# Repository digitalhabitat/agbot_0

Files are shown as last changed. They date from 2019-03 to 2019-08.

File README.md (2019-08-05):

# agbot_0

IUPUI's robot for the 2019 Mining for Microbes and Microfauna Agbot Challenge

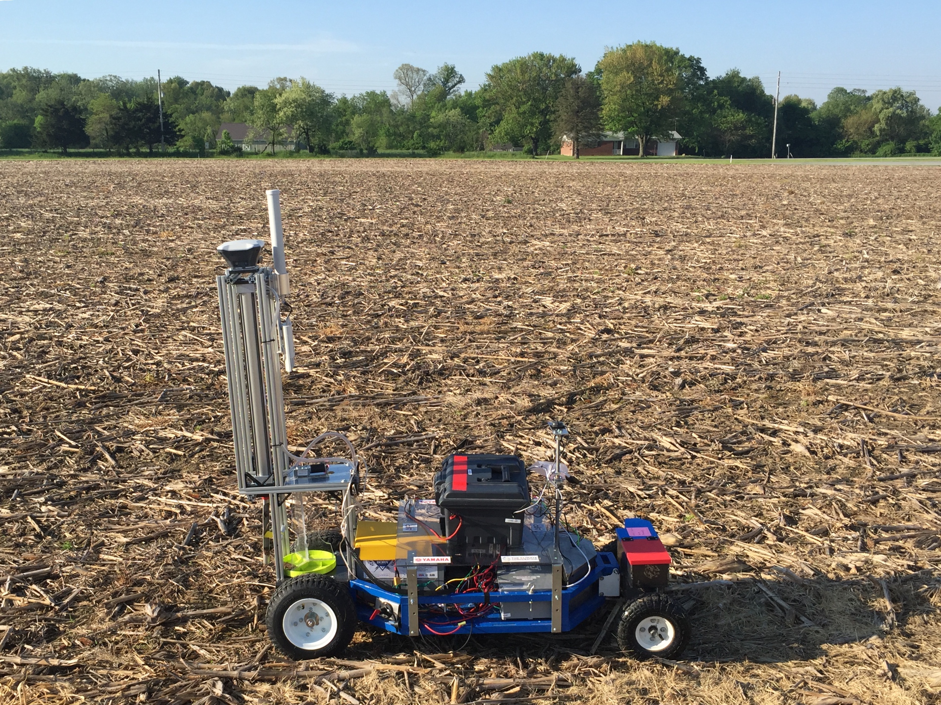
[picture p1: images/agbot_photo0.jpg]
AgBot Photo


## Quick start up

To get the agbot moving perform the following steps

0. Switch on the 12 volt Logic battery by fliping the amber rocker switch inside the tool box encolsure.
1. Turn on the Nvidia TX2 by pressing the right most button. (Green LED on TX2 will light)
2. Connect a computer or phone to the TX2 hotspot or the local wifi 
3. Switch on the AgBot's main power by turning the red mounted E-Switch. (Clockwise) ***THIS IS THE ONBOARD EMERGENCY STOP***
4. Switch on the *Lejin Wireless Relay* power located on the Power Box. (White LED on Wireless relay box will light)
5. On the *Lejin Wireless Remote* press button 1. (White LED on Power Box will light). ***THIS IS THE WIRELESS EMERGENCY STOP***
6. Connect to the TX2 via SSH `ssh nvidia@tegra-ubuntu` (If using a phone use the Terminus App)
7. Turn on the PS4 controller
8. In the terminal enter `checkusb` (This verifies the drive and steering system is ready)
9. In the terminal enter `roslaunch agbot_0 rc.launch` ( Ctrl-C to terminate program)
10. Holding ✕... To drive forward gently press R2. To drive reverse gently press L2. Use left joystick to steer.
11. On the *Lejin Wireless Remote* button 2 will close the solenoid for the air tank to build pressure (Not necessary to penetrate soft soil). 
Button 3 will extend/retract the soil probe.
## Table of Contents

[Precautions and Troubleshooting](https://github.com/digitalhabitat/agbot_0#precautions-and-troubleshooting)

[Local Machine Setup](https://github.com/digitalhabitat/agbot_0#local-machine-setup)

[ROS Packages & Launch files (To run on the agbot runing roscore)](https://github.com/digitalhabitat/agbot_0#ros-packages--launch-files-to-run-on-the-agbot-runing-roscore)

[ROS Packages & Launch files (To run on remote PC)](https://github.com/digitalhabitat/agbot_0#ros-packages--launch-files-to-run-on-remote-pc)

[Main System and Hardware Devices](https://github.com/digitalhabitat/agbot_0#main-systems-and-hardware-devices)

[Abstract Diagram](https://github.com/digitalhabitat/agbot_0#abstract-hardware-diagram)

[Wiring Diagram](https://github.com/digitalhabitat/agbot_0#wiring-diagram)

## Precautions and Troubleshooting

+ The agbot does not stop moving or shows delayed control
	+ The Drive motors will go into a run away state if the wheel encoders are disconnected or intermittent. Ensure that the wheel encoder wire connections are properly attached and secure. Verify safe functionality on a jack stand before operating on the the lab floor. Always be ready to press button 1 on the wireless relay remote to activate the Emergency Stop in case this event occurs. ***NEVER STAND DIRECTLY IN FRONT OR BEHIND THE AGBOT***
	+ The PID controller configuration may need additional tunning. See [BasicMicro Motion Studio](https://www.basicmicro.com/downloads)
	+ Delayed control around 1-2 sec at worst is typical.

+ `ssh nvidia@tegra-ubuntu` is not working
	+ The IP address of the TX2 is liable to changing. It might be necessary to accesses the local wifi router setup page or use a network scanner app to verify the IP address of the TX2 replacing `ssh nvidia@tegra-ubuntu` with `ssh nvidia@192.168.X.XXX` This IP address can be mapped to the hostname `tegra-ubuntu` by appending `etc/hosts` file on Linux.
	+ It maybe neccesary physically log onto the machine and verify network connenction with Ubiquity antenna. 

+ The TX2 does not turn on
	+ Ensure the Batteries are fully charged
	+ Check Voltage at the ouput of the 12V regulator.
	+ Check Fuse
	+ Disconnect the barrel plug on the TX2 and wait 15 seconds then reconnect the barrel plug
	+ Attach Battery to Charger while attempting to turn on the TX2
	+ Use diffently Power Suppply. Sometimes the LiFePO4 battery is more reliable.

+ The TX2 loses power when operating
	+ The TX2 and be powered by either the LiFePO4 battery or the Lead Acid Battery. The drive motors can cause system brown-outs on the LiFePO4 Power Supply. To avoid the TX2 reseting, use the Lead-Acid Batteries or a separate Power Supply.

+ The PS2 controller is not working
	+ The PS2 controller may need to be charged. A glowing orange light will indicate it is properly charging.

+ `catkin buid` is failing
	+ the dependencies have not been properly updated in 'agbot_0/package.xml' for this project. You may need to inspect the build error message to figure out which software package could not be found. The solution usually looks something like this... `sudo apt install ros-kinetic-some_package` or `sudo apt install some_library` or you may be able to just run `rodep update`

+ The Drive motors are not working
	+ Run 'checkusb' and verify the Roboclaw is properly wired and recieving 12V
	+ Reset and/or Disconnect power
	+ Alternate usb ports or bypass the usb hub and connect directly to the tx2.
	+ The PID controller configuration may need additional tunning. See [BasicMicro Motion Studio](https://www.basicmicro.com/downloads)
	+ See [roboclaw_node](https://github.com/digitalhabitat/roboclaw_node)
		+ [roboclaw.launch](launch/include/roboclaw.launch)
	+ See [udev](https://github.com/digitalhabitat/agbot_0/tree/master/udev)
	+ Helpful commands `lsusb` `dmesg --follow` `tldr`

+ The Steering is not working
	+ Run 'checkusb' and verify the Jrk is properly and recieving 12V
	+ Reset and/or Disconnect power
	+ Alternate usb ports or bypass the usb hub and connect directly to the tx2.
	+ The PID controller configuration may need additional tunning. See [Jrk G2 Software](https://www.pololu.com/product/3147/resources)
	+ The verticle coupling attached to the linear actuator is susceptible to sliping. You may need to tighten this with a hex key.
	+ See [jrk_motor_node](https://github.com/digitalhabitat/jrk_motor_node)
		+ [jrk.launch](launch/include/jrk.launch)
	+ See [udev](https://github.com/digitalhabitat/agbot_0/tree/master/udev)
	+ Helpful commands `jrk2cmd --status --full` `lsusb` `dmesg --follow` `tldr`

+ `roslaunch agbot_0 main.launch` is not working
	+ `main.launch` and `ekf.launch` are the most pertinent files for this project. Locailization is has only been experimentally verified for this project. It will be neccesary to play with the parameters or comment out sections to pinpoint the root cause. `main.launch` was intended to be launch from a remote linux PC on the same newtork to use MapViz and other GUIs. The PS2 controller has yet to be configured to connect through the remote linux PC, so its range will be limited to Bluetooth.
	+ See [robot_localization](http://docs.ros.org/melodic/api/robot_localization/html/index.htm)
	
+ Emlid GPS is not working
	+ The Emlid GPS does not get a good enough signal inside the lab, the south side of the building outside usually works fine.
	+ Install Emlid Reach phone app or enter in the IP address in a browser to access the configurations
	+ The Emlid GPS currently can only use NTRIP services for INDOT RTK corrections directly over wifi. They eventually must be configured to connect the a wifi router that is on-board the Agbot or the TX2 configured as an Access Point/Hotspot to take advatage of the Ubiquity antenna network connection. However the wifi signal is usually good enough on the south side of the building. 
	+ A possible work around to recieve INDOT RTK corrections with the Emlid configured to receive corrections over USB is to use an NTRIP Client on the TX2 using `str2str` See (https://manpages.debian.org/unstable/rtklib/str2str.1.en.html)
	+ See [launch/test_gps.launch](https://github.com/digitalhabitat/agbot_0/blob/master/launch/test_gps.launch)
	+ See [udev](https://github.com/digitalhabitat/agbot_0/tree/master/udev) 
	+ Helpful commands `lsusb` `dmesg --follow` `tldr`

+ Phidgets IMU is not working
	+ This project had limited success with the accuracy of the Phidgets IMU use `rostopic listen` to verify data is recieved
	+ I may be better to setup and use Tinkerforge Brick 2.0 IMU in tandem 
	+ See [Phidgets User Guide](https://www.phidgets.com/?tier=3&catid=10&pcid=8&prodid=1158#Windows)
	+ See [Preparing Sensor Data]http://docs.ros.org/melodic/api/robot_localization/html/preparing_sensor_data.html

## Local Machine Setup  
File structure assumptions on tx2:
```
nvidia@tegra-ubuntu:~/catkin_ws/src$ ls
agbot_0  CMakeLists.txt  jrk_motor_node  roboclaw_node
```
File structure assumptions on local machine to roslaunch nodes remotely:
```
user@machine:~/catkin_ws/src$ ls
agbot_0  jrk_motor_node  mapviz  nmea_navsat_driver  roboclaw_node
```

To launch devices nodes remotely from a local machine on to the TX2:
```bash
$ export ROS_MASTER_URI='http://tegra-ubuntu.local:11311'
$ ros launch agbot_0 main.launch
```
***NOTE:*** "$ export ROS_MASTER_URI=" only needs to be run once for a given terminal. The following command can use to set the envirment variable for every new terminal.
```bash
echo "ROS_MASTER_URI=http://tegra-ubuntu.local:11311" >> ~/.bashrc 
```
This can also done by manually editing ~/.bashrc

## ROS Packages & Launch files (To run on the agbot runing roscore)
+ #### Roboclaw
	+ https://github.com/digitalhabitat/roboclaw_node
		+ [roboclaw.launch](launch/include/roboclaw.launch)

+ #### Steering Controller (Jrk G2 24v13)
	+ https://github.com/digitalhabitat/jrk_motor_node
		+ [jrk.launch](launch/include/jrk.launch)

+ #### Emlid Reach M+
	+ http://wiki.ros.org/nmea_navsat_driver (building from source, nmea_serial_driver)
		+ [emlid_gps.launch](launch/include/emlid_gps.launch)

+ #### PhidgetSpatial Precision 3/3/3 (1044_0B)
	+ http://wiki.ros.org/phidgets_imu
	+ http://wiki.ros.org/imu_filter_madgwick
		+ [phidget_imu.launch](launch/include/phidget_imu.launch)
	
+ #### Tinkerforge Brick 2.0 (Not yet utilized)
	+ https://github.com/droter/tinkerforge_imu_v2
		+ https://github.com/gus484/ros-tinkerforge_sensors

+ #### Playstation 4 Controller & Teleoperation (with bluetooth and ackermann-to-twist topic converserion nodes)
	+ http://wiki.ros.org/joy
	+ http://wiki.ros.org/joy_teleop
		+ [teleop.launch](launch/include/teleop.launch)

+ #### Localization (Sensor Fusion)
	+ http://wiki.ros.org/robot_localization
		+ [ekf.launch](launch/include/ekf.launch)

## ROS Packages & Launch files (To run on remote PC)
+ #### Vizualization
	+ http://wiki.ros.org/mapviz
	+ http://wiki.ros.org/rviz
		+ [mapviz.launch](launch/include/mapviz.launch)
		+ [rviz.launch](launch/include/rviz.launch)
	
+ #### Playstation 4 controller (launch file for Teleop over wifi not developed yet)

+ #### Debuging Tools
	+ http://wiki.ros.org/rqt_graph
	+ http://wiki.ros.org/rqt_tf_tree
	+ http://wiki.ros.org/rqt_robot_monitor
	+ http://wiki.ros.org/rqt_logger_level
	+ http://wiki.ros.org/rqt_console
		+ [tf_and_node.launch](launch/include/tf_and_node.launch)

## Main Systems and Hardware Devices

+ #### Computer System
	+ [Nvidia Jetson TX2](https://developer.nvidia.com/embedded/buy/jetson-tx2-devkit)
	+ [7-Port USB Hub](https://www.amazon.com/Anker-7-Port-Adapter-Charging-iPhone/dp/B014ZQ07NE)
	+ [Playstation DS4 Controller](https://www.amazon.com/DualShock-Wireless-Controller-PlayStation-Black-4/dp/B01LWVX2RG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)

+ #### Drive System (RWD)
	+ Motor Controller: [Roboclaw 2x60A](https://www.pololu.com/product/3289) 
	+ Motor Encoders: [US Digital (E2-500-375-NE-D-G-1)](https://www.usdigital.com/products/encoders/incremental/rotary/kit/E2)
	+ Motors: [AmpFlow Gearmotor (E30-400-G)](http://www.ampflow.com/ampflow_gearmotors.htm)

+ #### Steering System
	+ Linear Acutor w/ Feedback: [Glideforce LACT4P-12V-20](https://www.pololu.com/product/2305)
	+ Steering Controller: [Jrk G2 24v13](https://www.pololu.com/product/3147)

+ #### Odometry and Localization System
	+ GPS: [Emlid Reach M+](https://emlid.com/reach/)
	+ GPS: [Emlid Reach RS+](https://emlid.com/reachrs/)
	+ GPS Antenna: [Tallysman GNSS antenna for Reach M+](https://store.emlid.com/product/tallysman-multi-gnss-antenna/)
	+ IMU+Compass: [PhidgetSpatial Precision 3/3/3 (1044_0B)](https://www.phidgets.com/?tier=3&catid=10&pcid=8&prodid=1038)
	+ IMU+Compass: [Tinkerforge IMU Brick 2.0](https://www.tinkerforge.com/en/shop/bricks/imu-v2-brick.html)
	+ RTK Base Station: [INDOT RTK Corrections](https://incors.in.gov/rtk.aspx)
	+ Drive System Encoders
	+ Visual Odometry: [Intel RealSense D435](https://store.intelrealsense.com/buy-intel-realsense-depth-camera-d435.html)

+ #### Wireless Network System
	+ 5 GHz Radio: [Ubiquity Rocket M5](https://store.ui.com/collections/wireless/products/rocket-m5)
	+ Omnidirectional antenna: [Ubiquiti AMO-5G10](https://store.ui.com/collections/wireless/products/5ghz-airmax-omni-10dbi-rocket-kit)

+ #### Power System
	+ [12V LiFePO4 100 Ah Battery](https://battlebornbatteries.com/shop/12v-lifepo4-deep-cycle-battery/)
	+ 2x12V Lead-Acid 7Ah Batteries(For Computer and Roboclaw logic battery
)	
+ #### Mining System
	+ [Lejin Wireless Relay, 8 channel-12V](https://www.amazon.com/Lejin-Wireless-Multifunction-Empanender-Transmitter/dp/B07944GQ6C)
	+ 4-Way Solenoide: [McMaster-Carr 6124k287](https://www.mcmaster.com/6124k287)
	+ Motor Controller: [Roboclaw 2x15A](https://www.pololu.com/product/3285)
	+ Gear Motor: [uxcell DC 12 Motor](https://www.amazon.com/dp/B0788CMXGP/ref=twister_B07CSWCZRV?_encoding=UTF8&psc=1)

+ #### Early Testing Platform
	+ Raspberry Pi 3 B+ Flashed with Ubiquity Robotics Raspbeery Pi Image
	+ Steering Servo:
	+ Motor Controler: Roboclaw 2x15A
	+ Quadrature Encoder: JGA25-370-12V-201rpm (only encoder)
	+ GPS: Emlid Reach M+
	+ IMU + Compass: PhidgetSpatial Precision 3/3/3 (1044_0B)

## Abstract Hardware Diagram
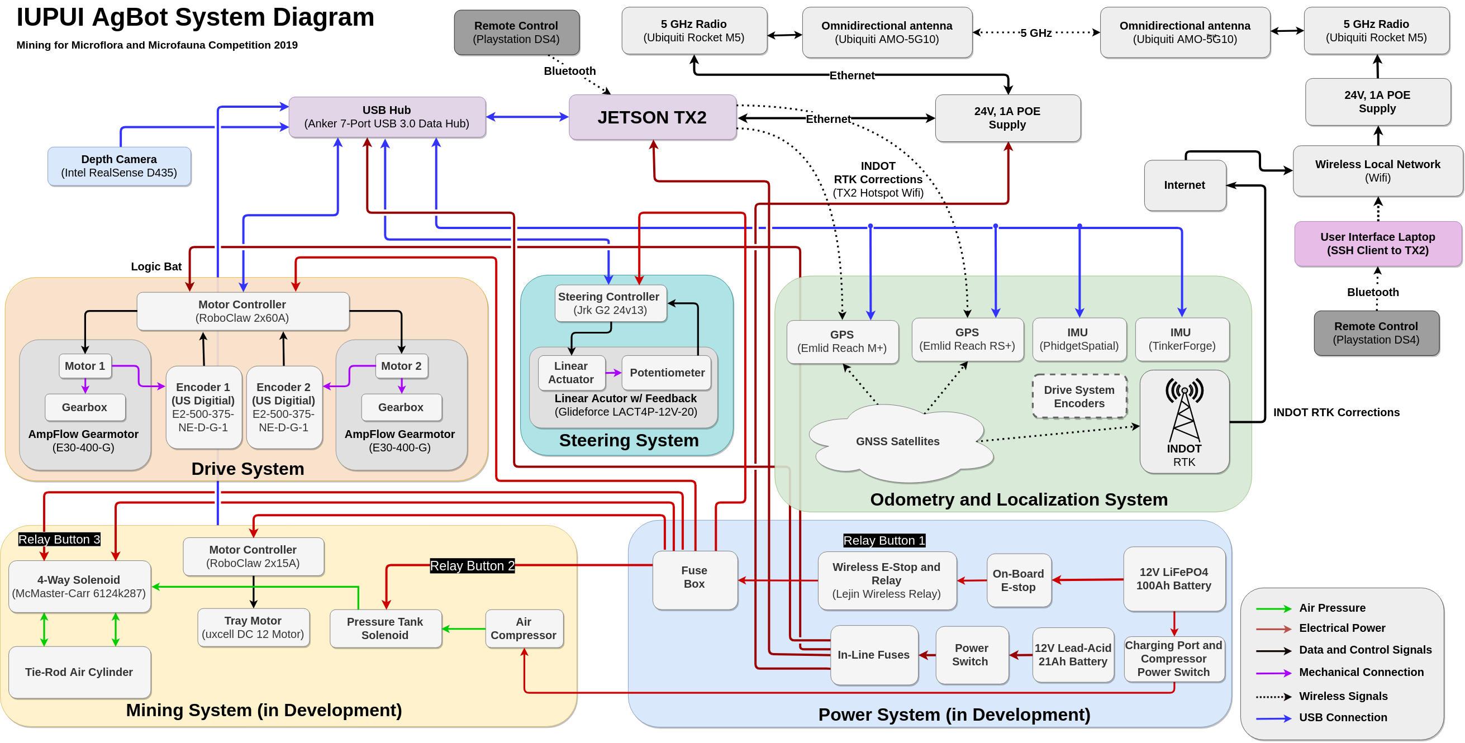
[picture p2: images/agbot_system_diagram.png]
HW_Diagram


[Click here](https://www.draw.io/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) to edit this image in a browser (?t=0 to bypass caches). Use the [Chrome App](https://chrome.google.com/webstore/detail/drawio-desktop/pebppomjfocnoigkeepgbmcifnnlndla) for native PNG+XML 

## Wiring Diagram
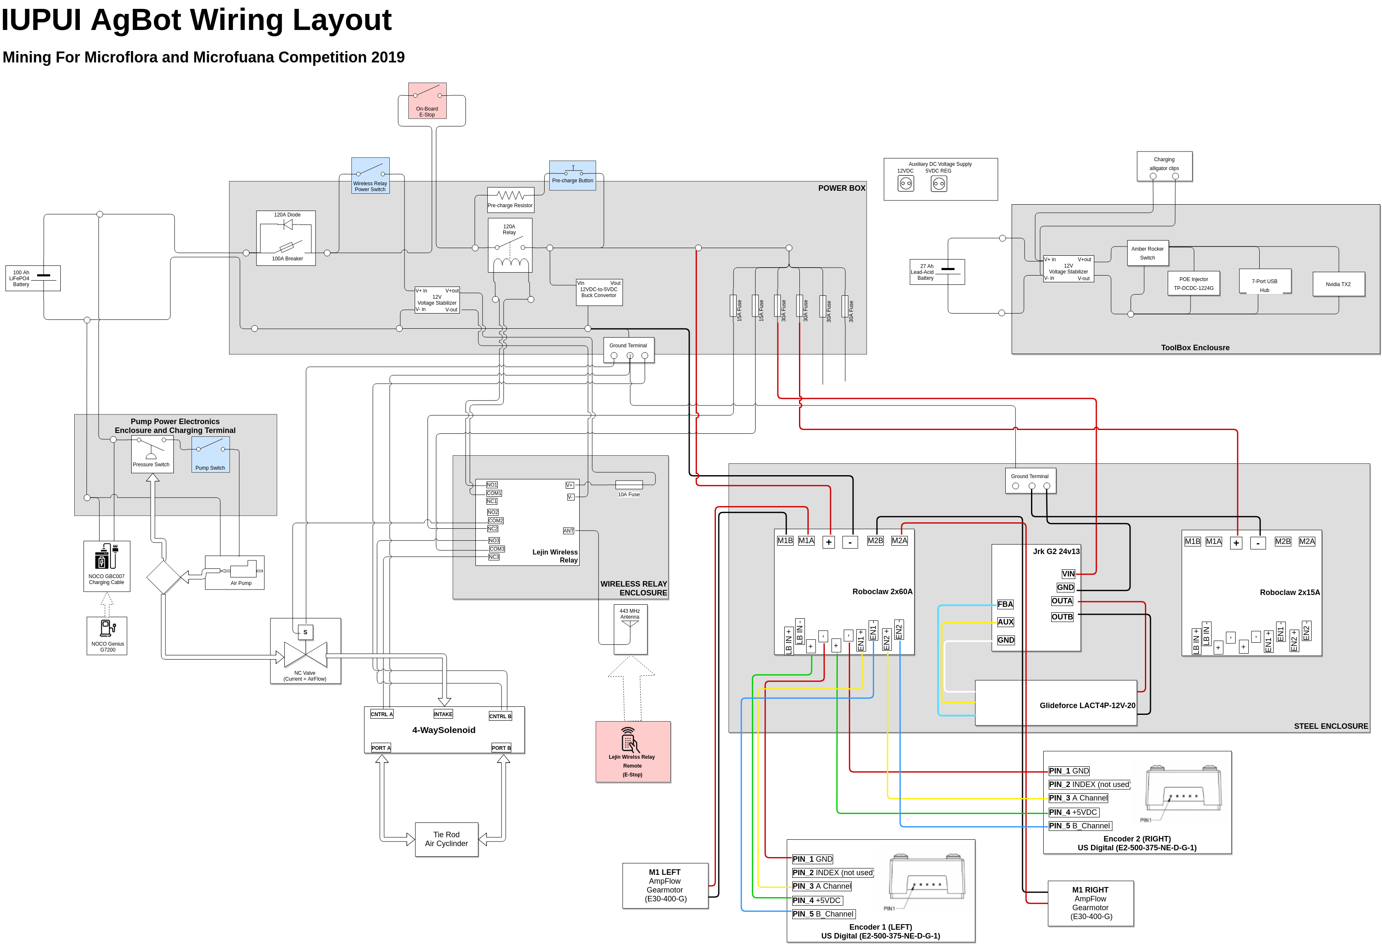
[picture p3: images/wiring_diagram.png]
HW_Diagram

[Click here](https://www.draw.io/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) to edit this image in a browser (?t=0 to bypass caches). Use the [Chrome App](https://chrome.google.com/webstore/detail/drawio-desktop/pebppomjfocnoigkeepgbmcifnnlndla) for native PNG+XML

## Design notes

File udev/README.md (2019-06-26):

 
### Using persistent device names
excute `setup-udev.sh` to copy udev rules file to `/etc/udev/rules.d/` directory

***Note: Some devices like the two emlid gps devices are differentiated only by
there placement on the usb hub. For example in the 99-emlidreach.rules file...***

`ATTRS{devpath}=="2.1"` means port 1 on the hub

`ATTRS{devpath}=="2.2"` means port 2 on the hub

####  Persistent Device names currently used
+ `/dev/reach_m_plus`
+ `/dev/reach_r_plus`
+ `/dev/roboclaw`

***Note: The jrk does not support persisentent naming. We can expect `/dev/ttyACM*`***

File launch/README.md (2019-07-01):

# agbot_0/launch/

### main.launch

This launch file is to be run on a the local pc and perform the following:

+ Launch ***mapviz*** on local pc

+ Launch ***rqt_logger_level*** on local pc (optional)

+ Launch ***rqt_console*** on local pc (optional)

+ Launch ***efk.launch*** on tx2

  + Contains robot_localization nodes and tf tranforms

+ Launch ***jrk.launch*** on tx2

  + Steering acuator

+ Launch ***teleop.launch*** on tx2

  + Nodes necessary for agbot control

+ Launch ***roboclaw.launch*** on tx2

  + Agbot drive drive control

+ Launch ***emlid_gps.launch*** on tx2

  + May requrie rtklib `str2str` to utilized INDOT RTK corrections over usb (else used local wifi network)

+ Launch ***pidget_imu.launch*** on tx2

  + Inconsitenly working

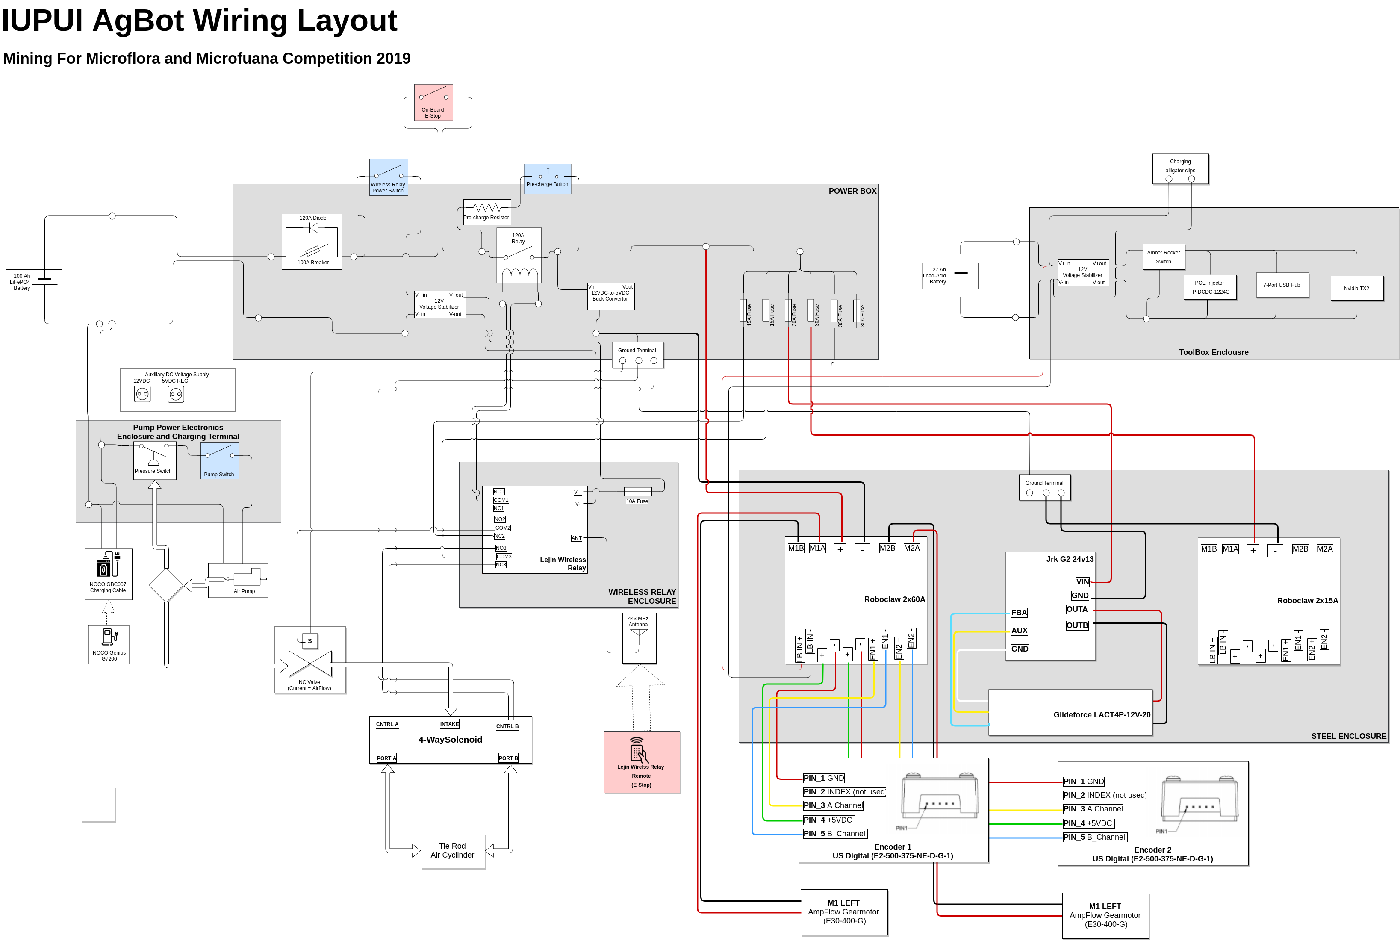
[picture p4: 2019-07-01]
images/detail_schematic.png

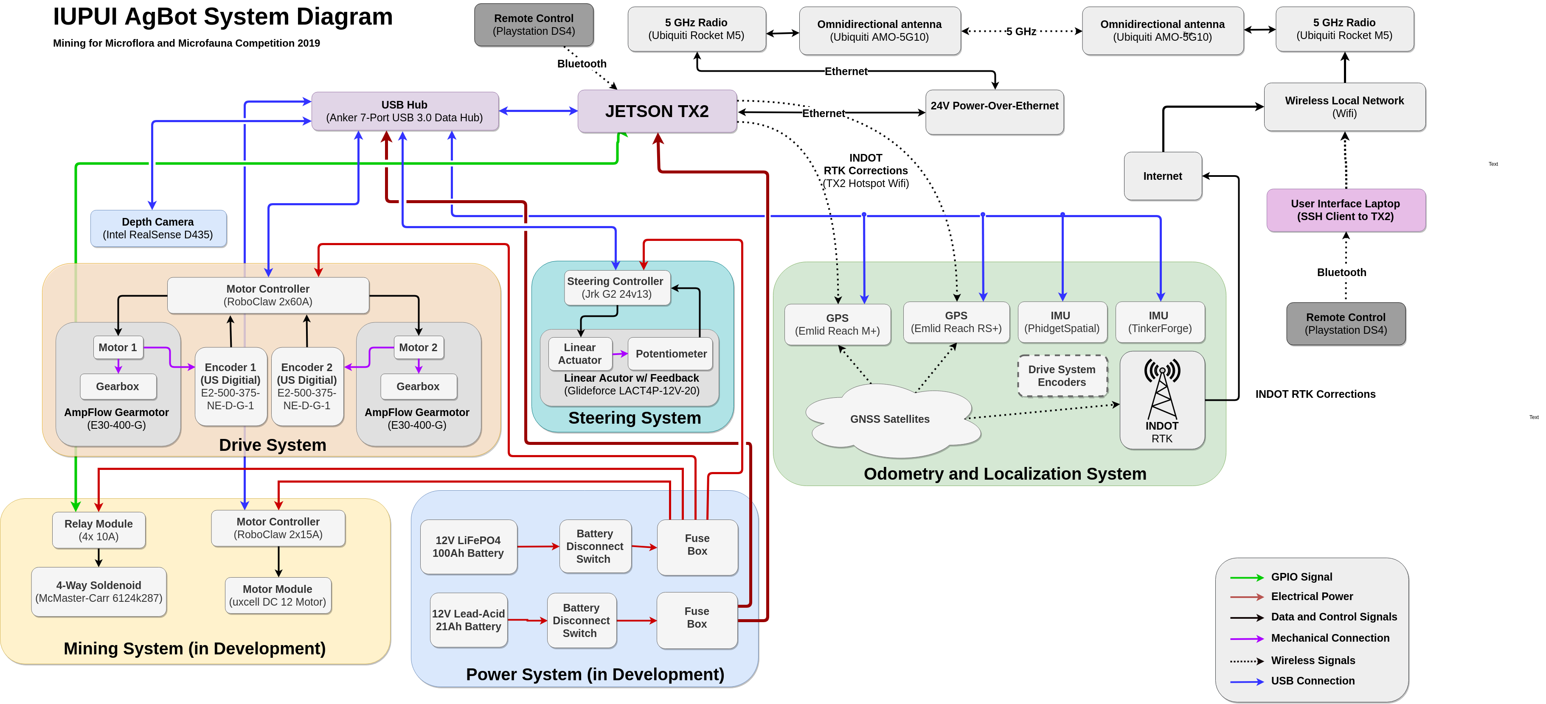
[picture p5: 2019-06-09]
images/AgBot_System_Diagram_Jun_8.png

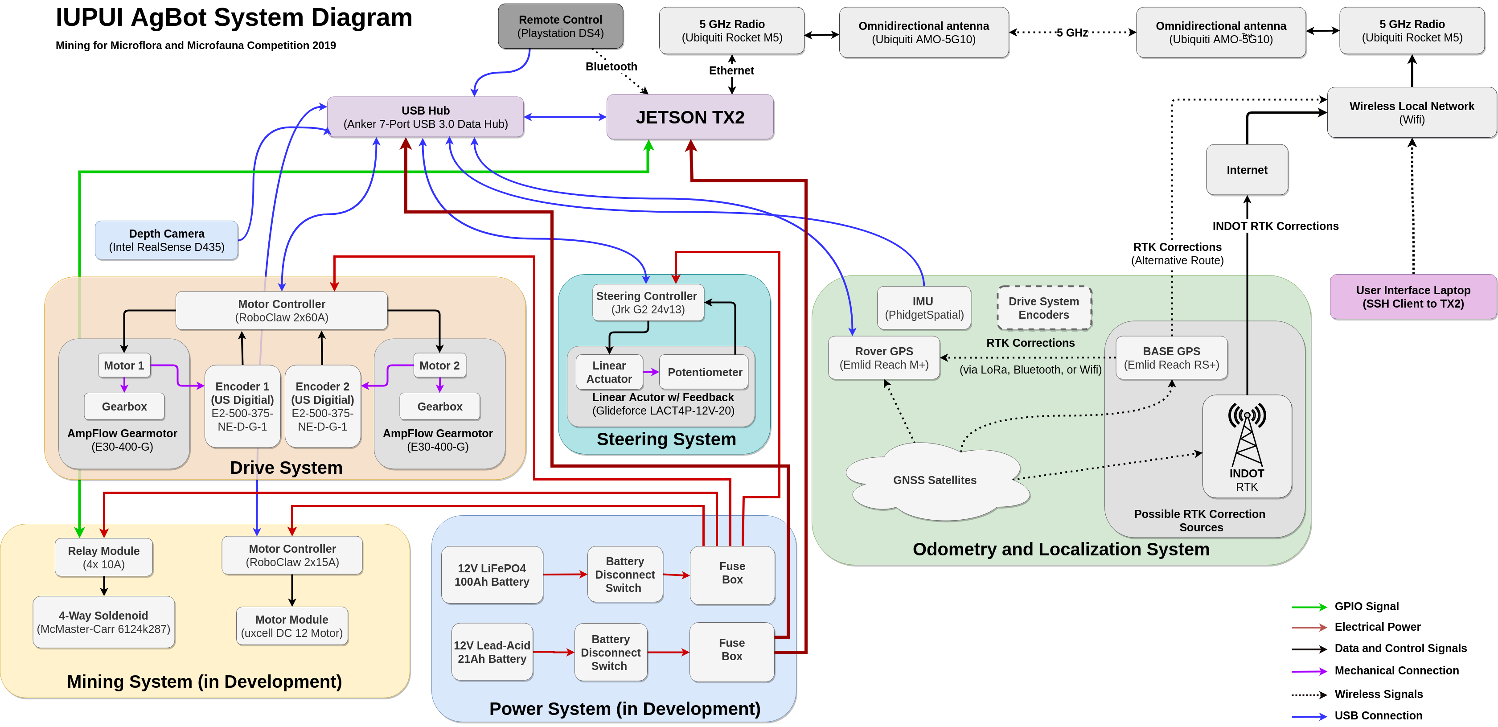
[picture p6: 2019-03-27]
images/agbot_hw_system_diagram.png

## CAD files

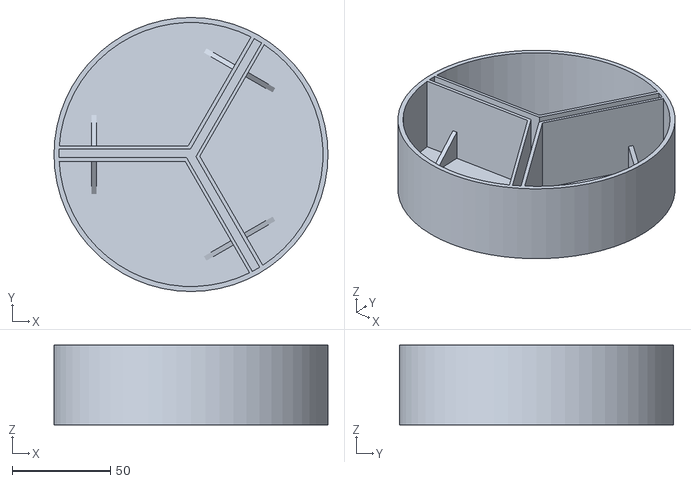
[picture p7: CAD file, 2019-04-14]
meshes/sorting_tray_centered.stl
139.7 x 139.7 x 40.6

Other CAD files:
meshes/Small Sorting Tray Base STL.stl
meshes/sorting_tray.stl
meshes/sorting_tray with spaces.stl

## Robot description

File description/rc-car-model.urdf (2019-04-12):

<?xml version="1.0" ?>
<!-- =================================================================================== -->
<!-- |    This document was autogenerated by xacro from rc-car-model.xacro             | -->
<!-- |    EDITING THIS FILE BY HAND IS NOT RECOMMENDED                                 | -->
<!-- =================================================================================== -->
<!-- A simple model of the rc-car for rviz -->
<!-- urdf-viz for quick viewing-->
<robot name="rc-car" xmlns:xacro="http://www.ros.org/wiki/xacro">
  <material name="black">
    <color rgba="0.2 0.2 0.2 1"/>
  </material>
  <material name="blue">
    <color rgba="0.3 0.57 1. 1"/>
  </material>
  

  ### base link
  
  <link name="base_link">
    <visual>
      <origin xyz="0.111 0 0.125"/>
      <geometry>
        <box size="0.222 0.1 0.11"/>
      </geometry>
      <material name="blue"/>
    </visual>
  </link>
  

  ### laser
  
  <joint name="base_to_laser_model" type="fixed">
    <parent link="base_link"/>
    <child link="laser_model"/>
    <origin xyz="0.275 0 0.205"/>
  </joint>
  <link name="laser_model">
    <visual>
      <geometry>
        <cylinder length="0.05" radius="0.026"/>
      </geometry>
      <material name="black"/>
    </visual>
  </link>
  

  ### Back left wheel
  
  <joint name="base_to_back_left_wheel" type="continuous">
    <parent link="base_link"/>
    <child link="back_left_wheel"/>
    <origin xyz="0 0.1025 0.06"/>
    <axis xyz="0 1 0"/>
  </joint>
  <link name="back_left_wheel">
    <visual>
      <geometry>
        <cylinder length="0.055" radius="0.06"/>
      </geometry>
      <material name="black"/>
      <origin rpy="1.57079632679 0 0"/>
    </visual>
  </link>
  

  ### Back right wheel
  
  <joint name="base_to_back_right_wheel" type="continuous">
    <parent link="base_link"/>
    <child link="back_right_wheel"/>
    <origin xyz="0 -0.1025 0.06"/>
    <axis xyz="0 1 0"/>
  </joint>
  <link name="back_right_wheel">
    <visual>
      <geometry>
        <cylinder length="0.055" radius="0.06"/>
      </geometry>
      <material name="black"/>
      <origin rpy="1.57079632679 0 0"/>
    </visual>
  </link>
  

  ### Front right wheel
  
  <joint name="base_to_front_left_hinge" type="continuous">
    <parent link="base_link"/>
    <child link="front_left_hinge"/>
    <origin xyz="0.222 0.1025 0.06"/>
    <axis xyz="0 0 1"/>
  </joint>
  <link name="front_left_hinge"/>
  <joint name="front_left_hinge_to_wheel" type="continuous">
    <parent link="front_left_hinge"/>
    <child link="front_left_wheel"/>
    <axis xyz="0 1 0"/>
    <orign xyz="0 0.0275 0"/>
  </joint>
  <link name="front_left_wheel">
    <visual>
      <geometry>
        <cylinder length="0.055" radius="0.06"/>
      </geometry>
      <material name="black"/>
      <origin rpy="1.57079632679 0 0"/>
    </visual>
  </link>
  

  ### Front left wheel
  
  <joint name="base_to_front_right_hinge" type="continuous">
    <parent link="base_link"/>
    <child link="front_right_hinge"/>
    <origin xyz="0.222 -0.075 0.06"/>
    <axis xyz="0 0 1"/>
  </joint>
  <link name="front_right_hinge"/>
  <joint name="front_right_hinge_to_wheel" type="continuous">
    <parent link="front_right_hinge"/>
    <child link="front_right_wheel"/>
    <axis xyz="0 1 0"/>
    <origin xyz="0 -0.0275 0"/>
  </joint>
  <link name="front_right_wheel">
    <visual>
      <geometry>
        <cylinder length="0.055" radius="0.06"/>
      </geometry>
      <material name="black"/>
      <origin rpy="1.57079632679 0 0"/>
    </visual>
  </link>
</robot>

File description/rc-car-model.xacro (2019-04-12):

<?xml version="1.0"?>

<!-- A simple model of the rc-car for rviz -->
<!-- urdf-viz for quick viewing-->

<robot xmlns:xacro="http://www.ros.org/wiki/xacro" name="rc-car">

  <xacro:property name="wheelbase" value="0.222" />
  <xacro:property name="width" value="0.100" />
  <xacro:property name="height" value="0.110" />
  <xacro:property name="ground_offset" value="0.070" />
  <xacro:property name="wheel_offset" value="0.025" />
  <xacro:property name="wheel_radius" value="0.06" />
  <xacro:property name="wheel_length" value="0.055" />
  <xacro:property name="laser_distance_from_base_link" value="0.275" />
  <xacro:property name="laser_height" value="0.05" />
  <xacro:property name="laser_radius" value="0.026" />

  <material name="black">
    <color rgba="0.2 0.2 0.2 1"/>
  </material>

  <material name="blue">
    <color rgba="0.3 0.57 1. 1"/>
  </material>

  ### base link
  <link name="base_link">
    <visual>
      <origin xyz="${wheelbase/2} 0 ${ground_offset+height/2}"/>
      <geometry>
        <box size="${wheelbase} ${width} ${height}"/>
      </geometry>
      <material name="blue"/>
    </visual>
  </link>

  ### laser
  <joint name="base_to_laser_model" type="fixed">
    <parent link="base_link"/>
    <child link="laser_model"/>
    <origin xyz="${laser_distance_from_base_link} 0 ${ground_offset+height+(laser_height/2)}"/>
  </joint>

  <link name="laser_model">
    <visual>
      <geometry>
        <cylinder radius="${laser_radius}" length="${laser_height}"/>
        <!--mesh filename="package://agbot_0/meshes/sorting_tray_centered.stl" scale="0.001 0.001 0.001"-->
      </geometry>
      <material name="black"/>
    </visual>
  </link>

  ### Back left wheel
  <joint name="base_to_back_left_wheel" type="continuous">
    <parent link="base_link"/>
    <child link="back_left_wheel"/>
    <origin xyz="0 ${(wheel_length+width)/2+wheel_offset} ${wheel_radius}"/>
    <axis xyz="0 1 0"/>
  </joint>

  <link name="back_left_wheel">
    <visual>
      <geometry>
        <cylinder radius="${wheel_radius}" length="${wheel_length}"/>
      </geometry>
      <material name="black"/>
      <origin rpy="${pi/2} 0 0"/>
    </visual>
  </link>

  ### Back right wheel
  <joint name="base_to_back_right_wheel" type="continuous">
    <parent link="base_link"/>
    <child link="back_right_wheel"/>
    <origin xyz="0 ${-(wheel_length+width)/2-wheel_offset} ${wheel_radius}"/>
    <axis xyz="0 1 0"/>
  </joint>

  <link name="back_right_wheel">
    <visual>
      <geometry>
        <cylinder radius="${wheel_radius}" length="${wheel_length}"/>
      </geometry>
      <material name="black"/>
      <origin rpy="${pi/2} 0 0"/>
    </visual>
  </link>

  ### Front right wheel
  <joint name="base_to_front_left_hinge" type="continuous">
    <parent link="base_link"/>
    <child link="front_left_hinge"/>
    <origin xyz="${wheelbase} ${(wheel_length+width)/2+wheel_offset} ${wheel_radius}"/>
    <axis xyz="0 0 1"/>
  </joint>

  <link name="front_left_hinge"/>

  <joint name="front_left_hinge_to_wheel" type="continuous">
    <parent link="front_left_hinge"/>
    <child link="front_left_wheel"/>
    <axis xyz="0 1 0"/>
    <orign xyz="0 ${wheel_length/2} 0"/>
  </joint>

  <link name="front_left_wheel">
    <visual>
      <geometry>
        <cylinder radius="${wheel_radius}" length="${wheel_length}"/>
      </geometry>
      <material name="black"/>
      <origin rpy="${pi/2} 0 0"/>
    </visual>
  </link>

  ### Front left wheel
  <joint name="base_to_front_right_hinge" type="continuous">
    <parent link="base_link"/>
    <child link="front_right_hinge"/>
    <origin xyz="${wheelbase} ${-(width)/2-wheel_offset} ${wheel_radius}"/>
    <axis xyz="0 0 1"/>
  </joint>

  <link name="front_right_hinge"/>

  <joint name="front_right_hinge_to_wheel" type="continuous">
    <parent link="front_right_hinge"/>
    <child link="front_right_wheel"/>
    <axis xyz="0 1 0"/>
    <origin xyz="0 ${-(wheel_length)/2} 0"/>
  </joint>

  <link name="front_right_wheel">
    <visual>
      <geometry>
        <cylinder radius="${wheel_radius}" length="${wheel_length}"/>
      </geometry>
      <material name="black"/>
      <origin rpy="${pi/2} 0 0" />
    </visual>
  </link>

</robot>

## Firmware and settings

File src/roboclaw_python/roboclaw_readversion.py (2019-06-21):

import time
from roboclaw import Roboclaw

#Windows comport name
#rc = Roboclaw("COM9",115200)
#Linux comport name
rc = Roboclaw("/dev/roboclaw",115200)

rc.Open()

while 1:
	#Get version string
	version = rc.ReadVersion(0x80)
	if version[0]==False:
		print "GETVERSION Failed"
	else:
		print repr(version[1])
	time.sleep(1)

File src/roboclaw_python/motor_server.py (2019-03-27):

#!/usr/bin/env python
#testing custom roboclaw ROS node
import time
import rospy
from std_msgs.msg import String
from geometry_msgs.msg import Quaternion, Twist

DEFAULT_TWIST_CMD_TOPIC = "~twist_command"
#Windows comport name
#rc = Roboclaw("COM9",115200)
#Linux comport name

def handle_add_two_inits(req):
	print "Returning [%s + %s = %s]"%(req.a, req.b, (req.a + req.b))
	return AddTwoIntsResponse(req.a + req.b)

def add_two_ints_server():
	rospy.init_node('add_two_ints_server')
	s = rospy.Service('add_two_ints', MotorServer, handle_add_two_ints)
	print "Ready to add two ints."
	rospy.spin()

if __name__ == "__main__":
	print "running add_two_ints_server"
	add_two_ints_server()

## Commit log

2019-03-29 added launch files
    [block.urdf, block.urdf.xacro]
2019-03-29 added servo code
2019-04-06 Updated ekf mapviz urdf joystick files
2019-04-06 added new urdf model
    [rc-car-model.urdf, rc-car-model.xacro]
2019-04-12 updated 3d model, testing out various efk configs,added GUI config files, and slight modifications to launch files.
    [rc-car-model.urdf, rc-car-model.xacro]
2019-04-14 global ekf working, next step is to test out navigation, and misc 3d were added
    [LFinger11_0.10.stl, Link1-v2.stl, Small Sorting Tray Base STL.stl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]
2019-04-26 Commiting for TX2 integration compass sould be correct now keep in mind that iron containing material with affect accuracy
2019-05-07 launch file edits, and added udev rules and setup mapviz.launch has parameter for xy_init to test without gps working by using passing stutz as parameter instead of auto
    [LFinger11_0.10.stl, Link1-v2.stl]
2019-05-15 still trying to fix this la
    [teleop.py]
2019-05-17 Fix steering angle convention
    [teleop.py]
2019-07-01 Added wiring_diagram.png
2019-07-05 Updated wiring_diagram.png
2020-02-20 added launch file and urdf file for gazebo sim
    [master_sim.xacro, sim_model.xacro]
2020-03-11 working simulated sensor usion, see test_mapviz.launch
    [ackermann_generic_sim.xacro, gps.xacro, master.xacro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]
2020-03-15 added launch file to test gps and imu with ekf
